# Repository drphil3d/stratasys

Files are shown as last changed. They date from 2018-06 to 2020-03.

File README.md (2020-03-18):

# Stratasys Reprap Project

Open Source Stratasys Conversion

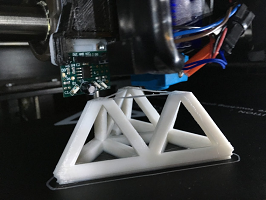
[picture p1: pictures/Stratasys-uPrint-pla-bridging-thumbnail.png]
Bridging Test


This was a long painful process, now that I've done the hard work it should be fairly easy for anyone to do this conversion. I'm not utilizing the stock hotends, they are designed for use with PC-ABS and other high temperature materials. At the moment I don't need dual extrusion, or the proprietary filament system which is far too complex. The results of this conversion is printer that makes consistent, strong parts with minimal effort.

If you plan to use the heated chamber above 40c you will need a water cooled hotend and extruder. I recommend using a Bondtech BMG - The Titan extruder was a nightmare, it requires disassembly to clear jams.

I recommend using a Ubis High Temperature hotend - 24v 90 Watt with a PT1000 and Thermistor
[Ubis Hotends](https://ubishotends.com/shop/xx9ppgi6moubdjx5kscfk8md4e8ecb)

##### Model Specific Firmware and Resources
   [Stratasys uPrint, uPrint SE / Plus](https://github.com/drphil3d/stratasys/tree/uPrint-SE)
   
   [Dimension 1200es SST / BST](https://github.com/drphil3d/stratasys/tree/Dimension-1200-SST)

Discussion
[Duet Forum](https://forum.duet3d.com/topic/10982/stratasys-uprint-retrofit-finally-complete/7)

#### Printer Control Board options

Ideally you want to use a board with decently powerful stepper drivers. Something in the 2amp range is preferable

##### DuetWifi
 -Pros
    Best option that matches the stepper drivers
    Sensorless Homing means no need to wire endstops
    Macro system is necessary for the extra features

 -Cons
    Display firmware doesn't support rotation of 90degrees
    Expensive
    
#### Klipper

 -Pros
   Use any board or combination of boards you want
   Super Fast Printing
   High Accuracy
   Customizable
   Macro Support
    
 -Cons
   Requires a raspberry pi or other embedded system

#### Marlin
 -Pros
   It works that was the first option I used on the uPrint

 -Cons
   Must be compiled and flashed every time you make a small change
   Most boards don't have stepper drivers that are powerful enough

#### Bake Oven temperature control
 The stock bake oven runs on 120VAC. Use an AC Solid State Rely to control the two heating elements. Keep in mind the heating elements can be wired for to operate at 120v ot 240v parallel or series.

 It is important that the fans spin whenever the heaters are energized.

 Make sure the heater safety shutoff switches operate correctly, If a fan stops spinning the heater will overheat without the shutoff switch. Do not remove them.

 This oven gets very hot under operation, I noticed the soldier on the OEM optical endstop PCB had melted and dripped down the board.
 Operating Temperature 0c - 75° C (167° F) Max

 Heating
    2x 120v DC 400 Watt (B075 CAT NO. FS2001G102) - Build Chamber Heaters one on each side
    2x 24V 0.48A Radial Blower Fans (blows air through the heating elements)
 Cooling   
    1x 24V Radial Blower Fan - Blows room temperature air onto the printhead and part from outside the build oven.

##### Gantry Information

 Depending on the model you may have more usable build area than what is immediately evident. The standard uPrint has a 152x152 build plate. However the printhead can reach outside of the build plate area to access more unused print volume. I believe the standard uPrint can accept two sizes of build platforms.

 Factory Specs
    uPrint 254 x 254 x 305 mm (10 x 10 x 12 in)
    Dimension SST 1200 SST X:254 Y:254 Z:305
 
 Actual Build Volume 
    uPrint X152 Y152 Z160

 Max Travel
    uPrint X280 Y262 Z150
    1200sst X:237.162 mm (9.33 in) Y:265.613 mm (10.45 in) Z:330.2 mm

 End Stops
    Use StallGuard sensorless homing and avoid all this madness, otherwise there are 2 optical endstops on each axis.

However another method is to tap into the test points the power distribution board if not already removed for the endstop signals   

  X-Min Y-Max Z-Max

Steps Per mm at 16x Microstepping
These seem to be accurate for the uPrint M92 X106.66 Y268 Z1011.99 E417
Z axis threaded rod is Imperial

Hardware
    XY 3mm belt pitch - 12mm GT3 Belts 16mm Linear Rods

 Belt / Gear Ratios
 uPrint
    X 16t x 60t x 20t (motor 16 tooth pulley) - (60 tooth pulley) - (20t drive shaft belt)
    Y 20t (20 tooth pulley) to (idler pulley)
    Z lead screw driven through motor mounted to bed
 1200 SST
    X (motor 16 tooth pulley) - (60 tooth pulley)
    Y (20 tooth pulley) to (idler pulley)
    Z (36 tooth pulley) to (36 tooth) to (big lead screw pitch unknown)
    
[More Hardware Specs](hardwarespecs.md)

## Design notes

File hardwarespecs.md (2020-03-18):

XY Axis Belt Specs

Gates 3MR-282-09 Belt
SKU 9390-4094
Part Number 3MR-282-09
Profile GT
Pitch	3 mm
Number of Teeth 94
Length (inch)	11.1
Length (mm)	282

Y Axis Small Belt

SDP A 6T53M280090
Bet Thickness 9mm
Pitch Length 840mm
Part Number: A 6R53M280090
Belt Type: Single Sided
Number of Grooves: 280
Belt Width: 9mm
Pitch Length: 840mm

GT®3 is an equivalent and direct replacement for GT®2 belts.
Neoprene - Nylon Covered, Fiberglass Reinforced
Breaking Strength: 158 N per 1 mm (113 lbf per 1/8 in.) 
Belt Width; not representative of the load-carrying capacity of the belt.
Working Tension:507 N for 25.4 mm belt (114 lbf for 1 in. belt).
Temperature Range: -34°C to +85°C (-30°F to +185°F)

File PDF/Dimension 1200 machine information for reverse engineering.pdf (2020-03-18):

Current Position The current X, Y and Z position in micro steps. X and Y = 16000 micro-steps per inch.
Z = 128000 micro-steps per inch.

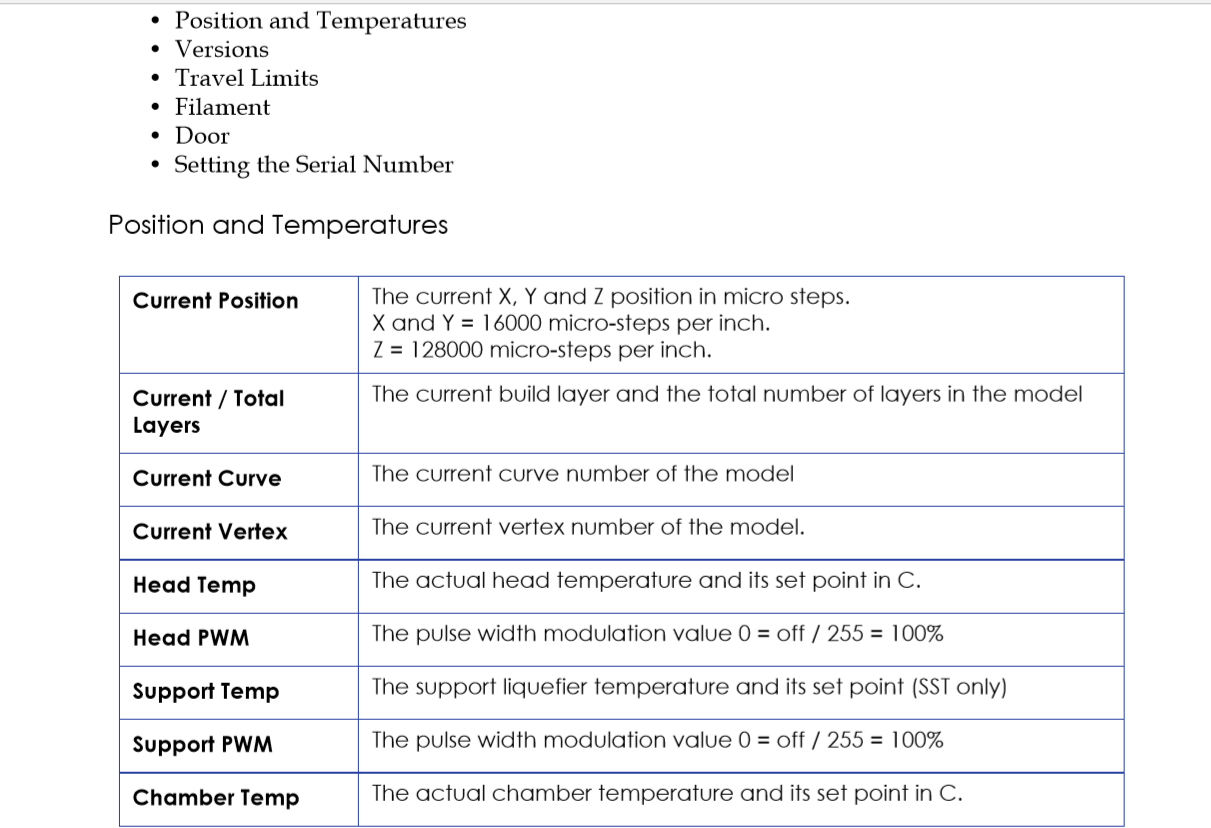
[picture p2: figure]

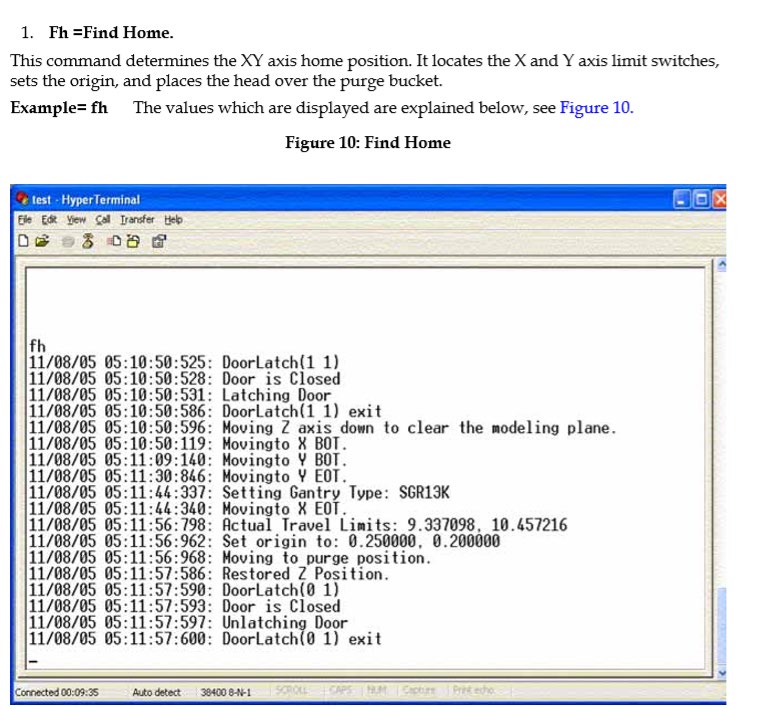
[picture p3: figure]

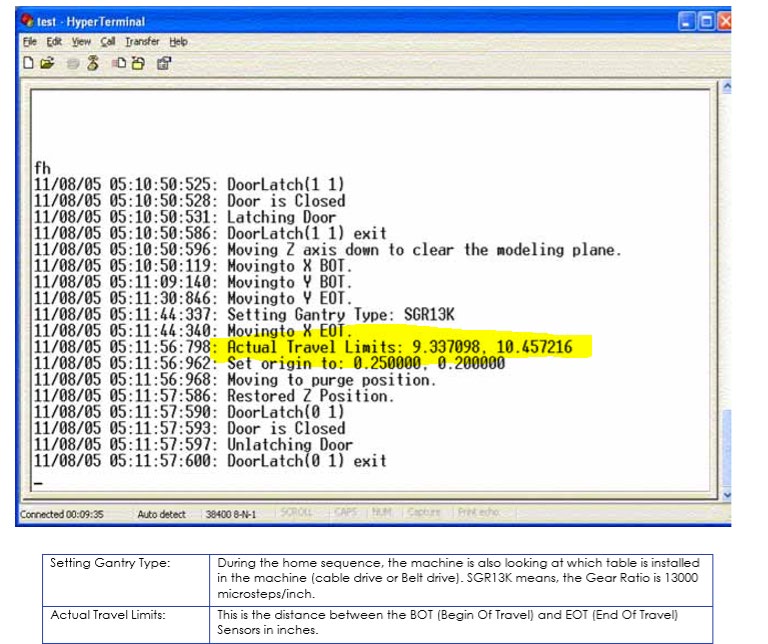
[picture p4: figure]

X:9.33 = 237.162mm Y: 10.45 = 265.613mm Origin 6.35 mm 5.08

X EOT 9.337098
Y EOT 10.457216

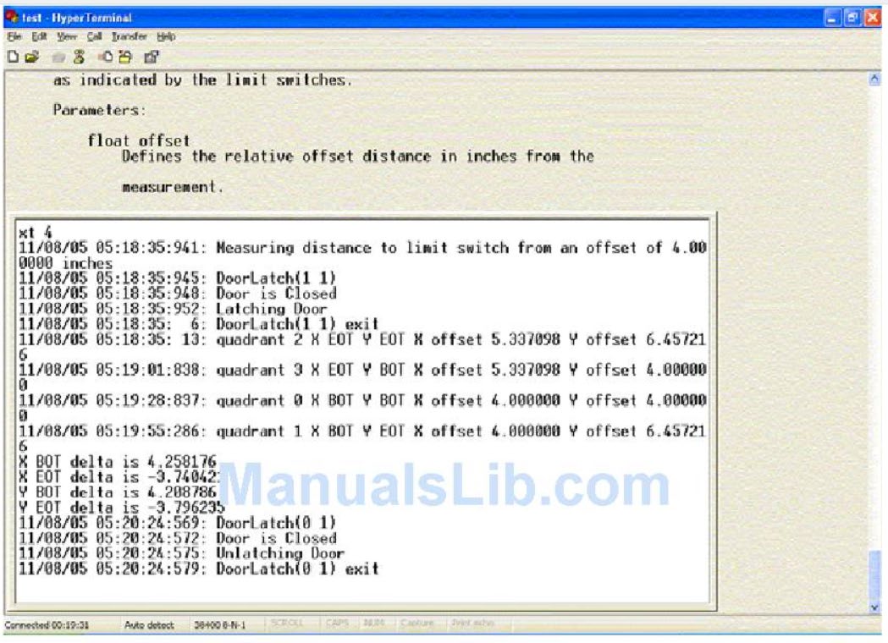
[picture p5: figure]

2 X offset 135.38
0 X offset 101.6 Y offset 101.6
1 X offset 101.6 Y offset 164.0131

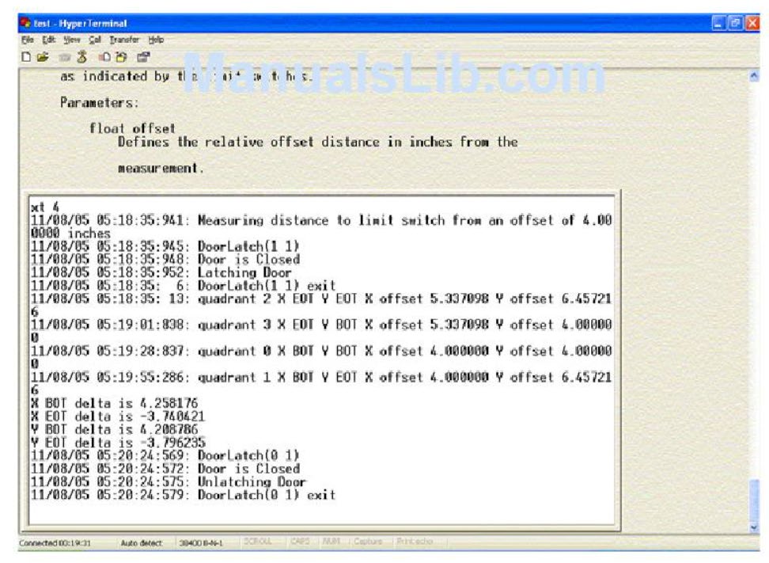
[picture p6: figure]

### 5. xt=Test XY Limits

Tests the XY axis by moving from corner to corner, stopping at each corner and measuring the offset against the actual position as indicated by the limit switches.
The command can be used for testing the Z-Stage. To do so, repeat the tz command at least 2 times and compare the X BOT delta values, X EOT delta values, Y BOT delta values and the Y EOT delta values. Parameters: Float Offset: Defines the relative offset distance in inches from the limit switch. The offset is the starting point for the measurement. Example= xt 2.0 2.0= distance, where the machine starts to look for the sensors. For repeating the command, type in the following: rt 2 1 "xt 2.0”. For more information see the rt command (item #8) in this manual.
Figure 13: Text XY limits

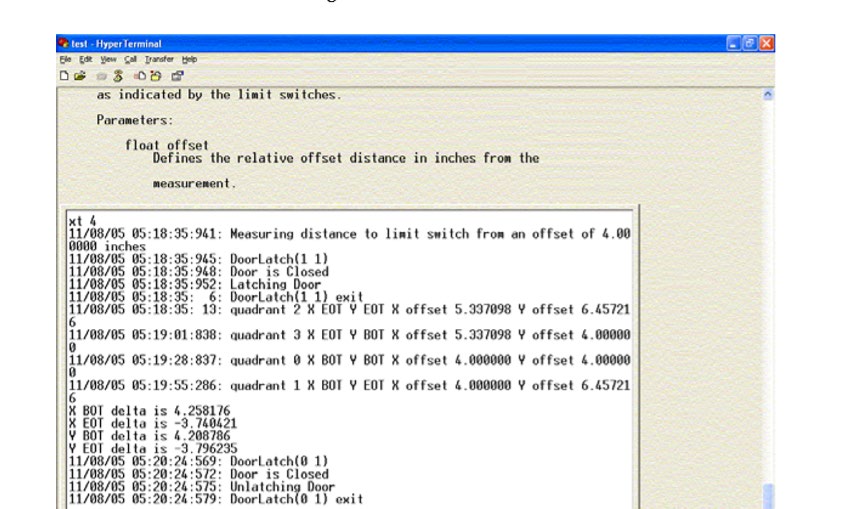
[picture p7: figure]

10. mx = move x This command moves the head in the X axis. Parameters: Float Position: This is the position it moves to, in inches, when the command is sent from the Console and in device units when the command is sent through the DPM.
Example: mx 3.0 (moves the X-Axis 3 inches away from the X-Home sensor

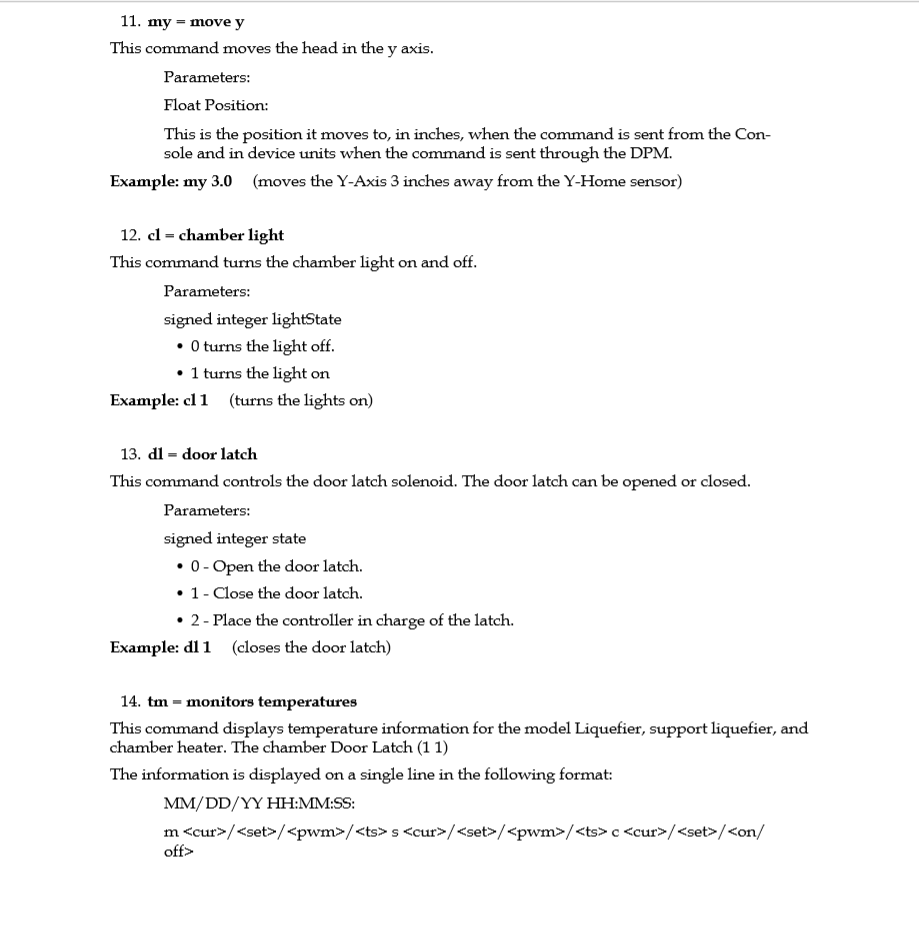
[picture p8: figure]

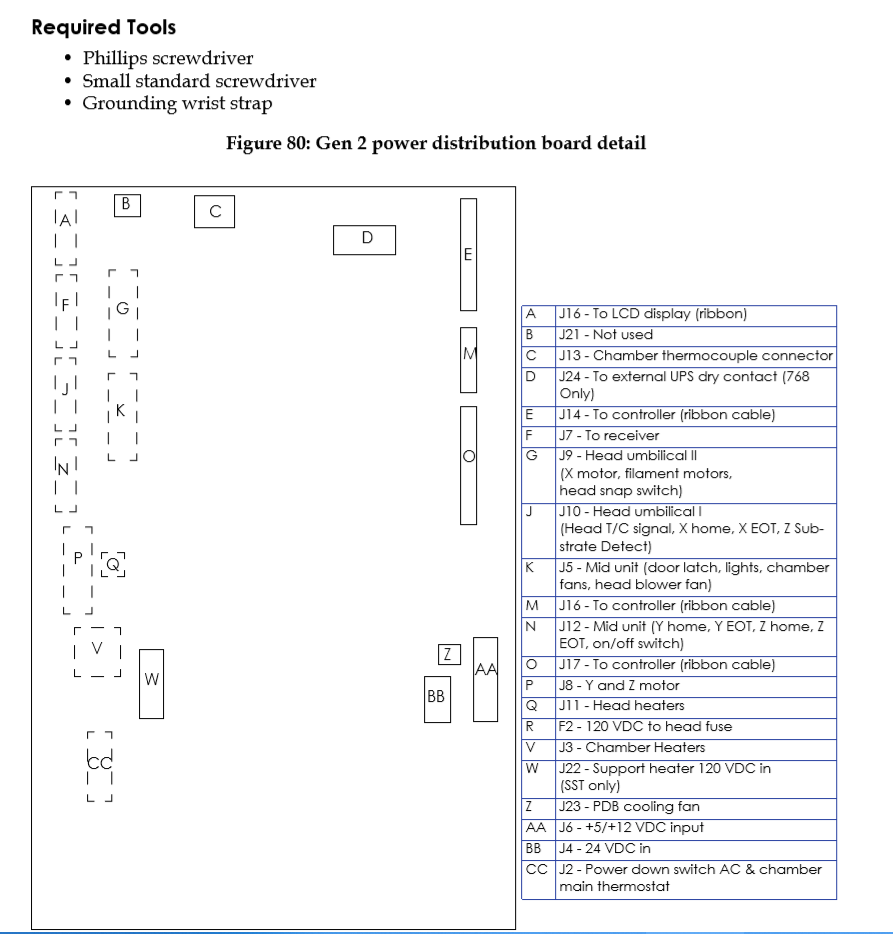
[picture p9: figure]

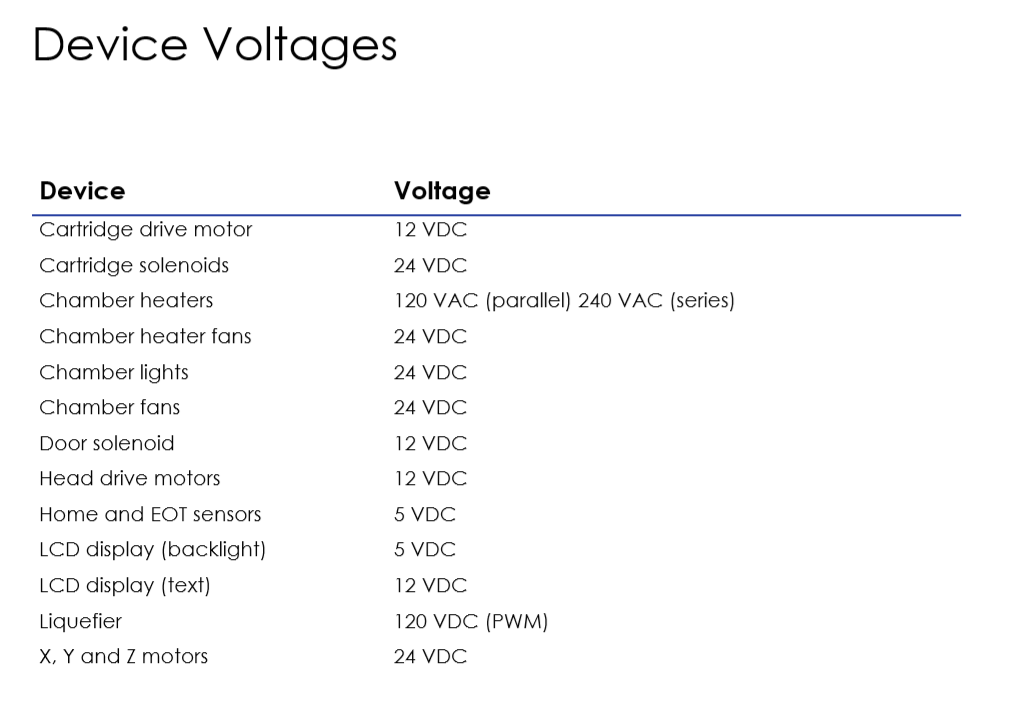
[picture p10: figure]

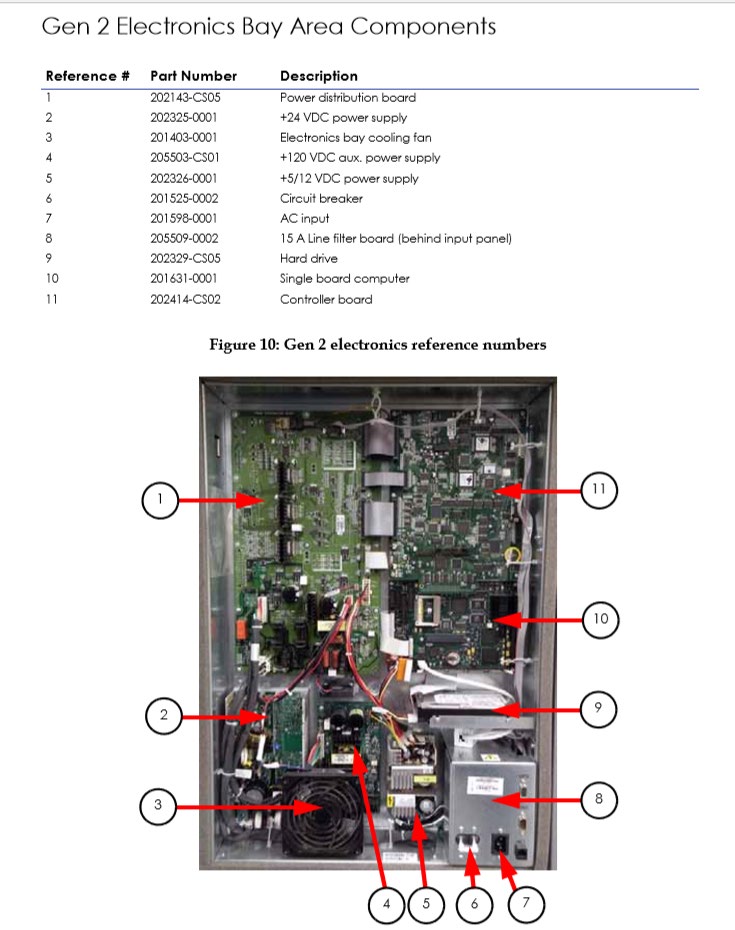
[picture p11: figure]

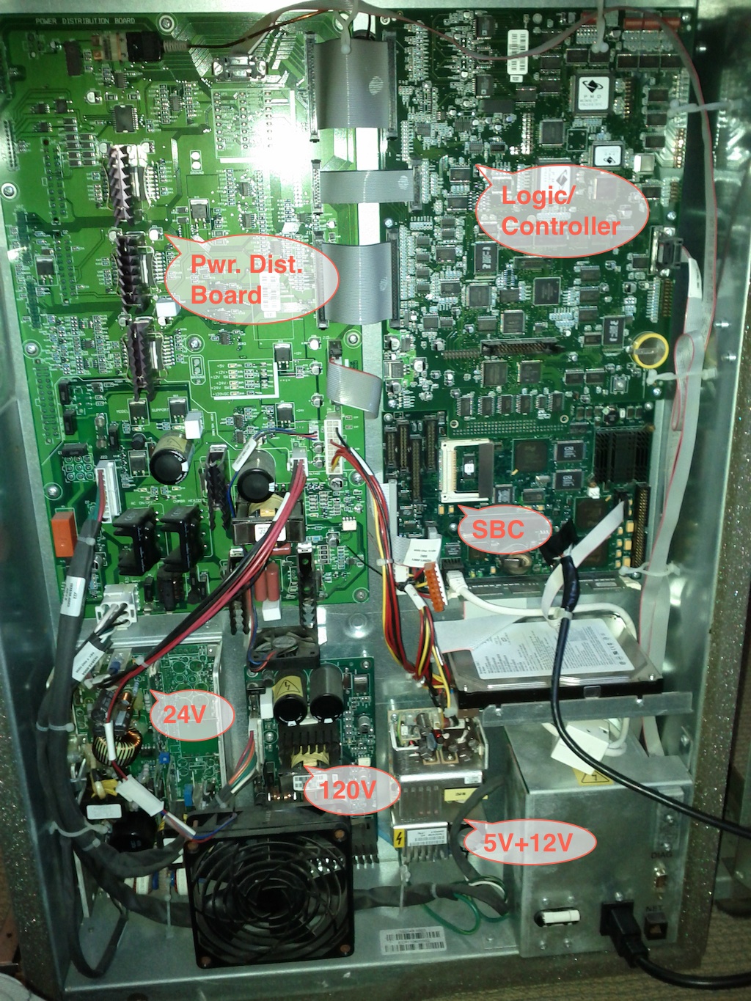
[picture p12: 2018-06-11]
pictures/dimension-sst-electronics-bay.jpg

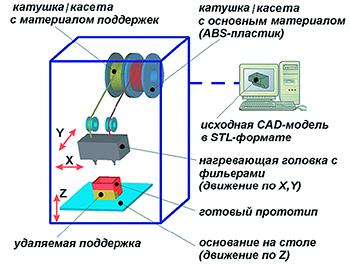
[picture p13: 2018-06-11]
pictures/stratasys_05.jpg

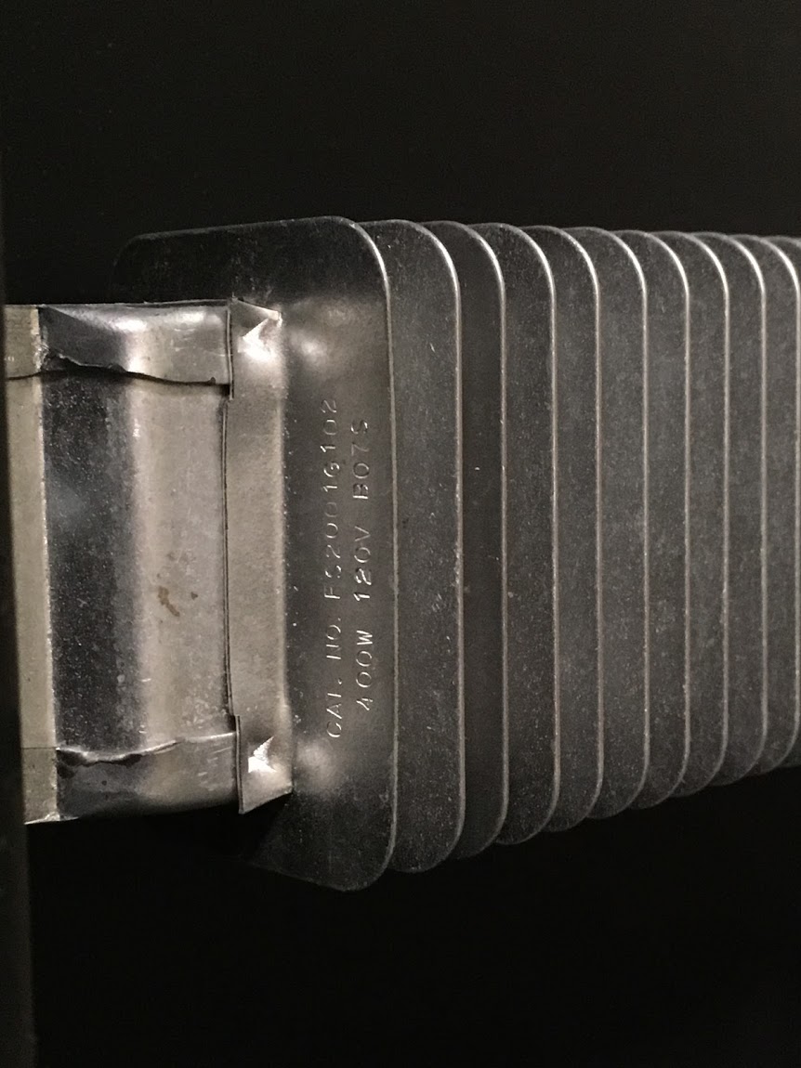
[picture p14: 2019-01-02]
pictures/heater.JPG

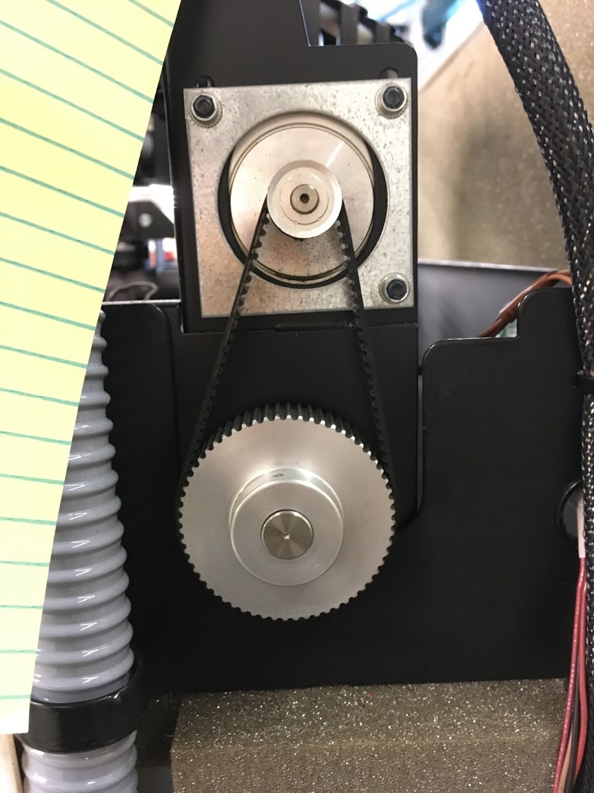
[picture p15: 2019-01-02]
pictures/y axis.JPG

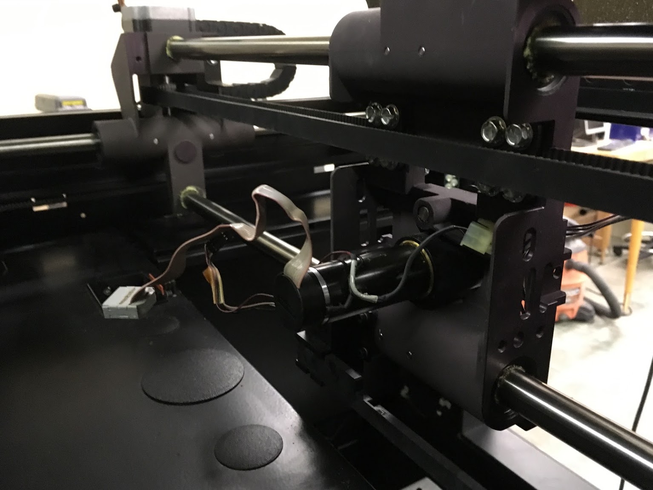
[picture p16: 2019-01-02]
pictures/y axis extruder.JPG

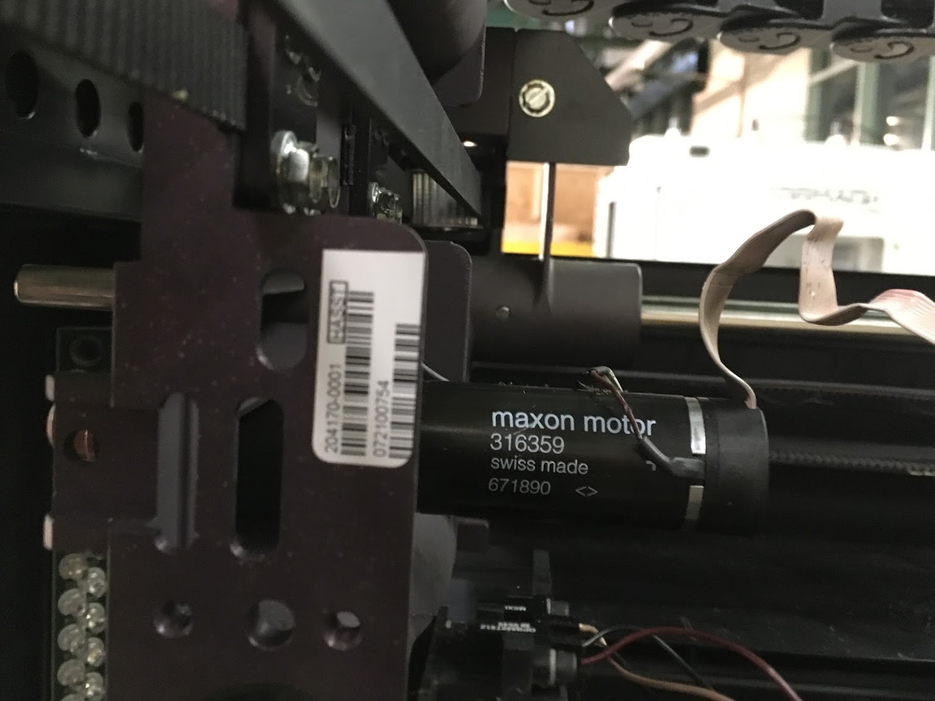
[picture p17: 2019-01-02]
pictures/extruder.JPG

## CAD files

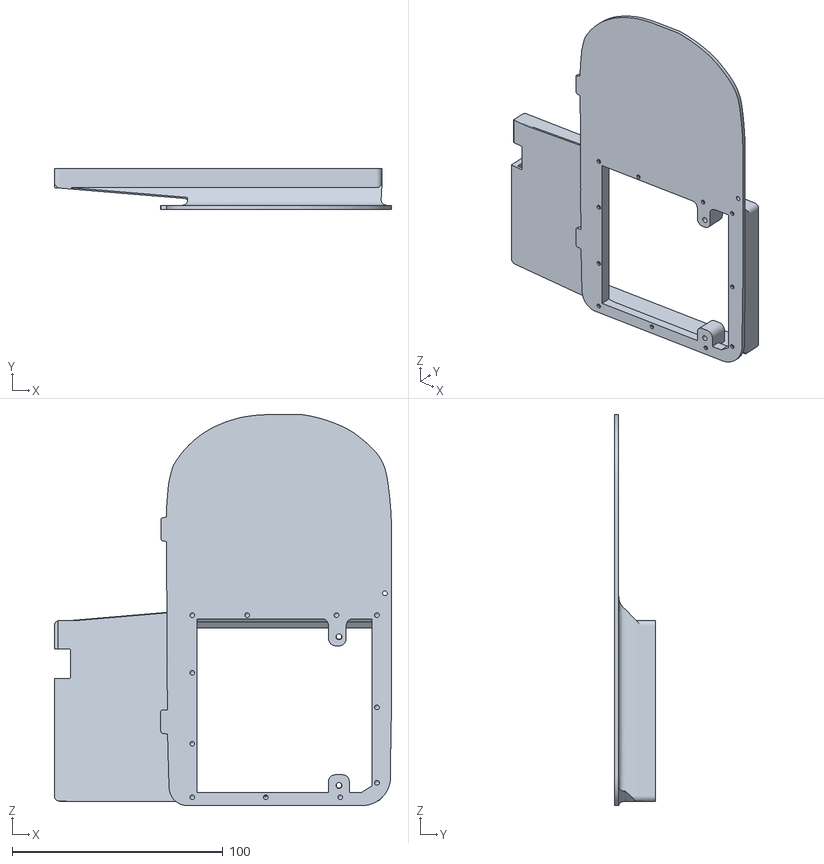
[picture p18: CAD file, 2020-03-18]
STL Files/Stratasys Panel Due.stl
160.2 x 19.2 x 185.6

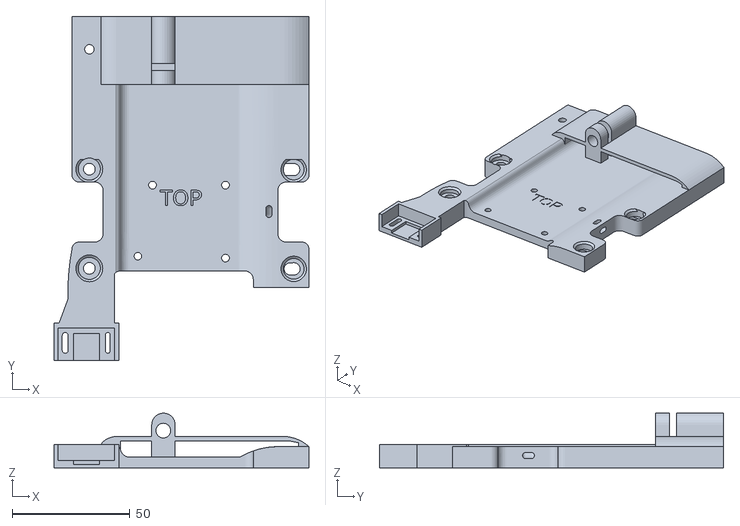
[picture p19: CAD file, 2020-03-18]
STL Files/Stratasys Printhead Mount.stl
108.3 x 146.2 x 23.2

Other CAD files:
CAD Files/6 to 4 mm adapter.f3d
CAD Files/EndStop Mount X+Z.f3d
CAD Files/EndStop Print Head Mount.f3d
CAD Files/Endstop Switch Mount.f3z
CAD Files/Print Head extruder Mounting Bracket.f3z
CAD Files/enstop mount.f3d
CAD Files/uPrint Front LCD.f3d
CAD Files/uPrint Hotend Adapter.f3d
CAD Files/uPrint Hotend Adapter.f3z

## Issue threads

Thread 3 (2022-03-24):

Belt titles are wrong

LazyTeenStudios, 2022-03-24:
In the readMe file the description for the small Y belt is under the title “XY axis belt specs” while the XY belt info is under the title “Y axis small belt.”

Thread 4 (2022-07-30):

Safety Thermistor Wiring

S1L3NTANG3L, 2022-07-30:
Just curious on how you ended up wiring the safety thermistors for the chamber heaters. Did you wire them in series with the heaters?

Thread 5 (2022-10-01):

Endstops

S1L3NTANG3L, 2022-10-01:
Hi
Did you use the oem optical end stops or did you replace them? (Uprint SE specifically).
Thanks

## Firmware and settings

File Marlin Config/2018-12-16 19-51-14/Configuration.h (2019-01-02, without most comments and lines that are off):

#pragma once
#define CONFIGURATION_H_VERSION 020000
#define STRING_CONFIG_H_AUTHOR "Dr. Phil3D"             // Who made the changes.
#define SHOW_BOOTSCREEN
#define STRING_SPLASH_LINE1 SHORT_BUILD_VERSION // will be shown during bootup in line 1
#define STRING_SPLASH_LINE2 WEBSITE_URL         // will be shown during bootup in line 2
#define SERIAL_PORT 0
#define BAUDRATE 250000
  #define MOTHERBOARD BOARD_EINSY_RETRO
#define CUSTOM_MACHINE_NAME "Stratasys"
#define MACHINE_UUID "b1910d4c-db07-11e8-9f8b-f2801f1b9fd1"
#define EXTRUDERS 1
#define DEFAULT_NOMINAL_FILAMENT_DIA 1.75
#define POWER_SUPPLY 0
#define TEMP_SENSOR_0 5
#define TEMP_SENSOR_1 0
#define TEMP_SENSOR_2 0
#define TEMP_SENSOR_3 0
#define TEMP_SENSOR_4 0
#define TEMP_SENSOR_5 0
#define TEMP_SENSOR_BED 1
#define TEMP_SENSOR_CHAMBER 0
#define DUMMY_THERMISTOR_998_VALUE 25
#define DUMMY_THERMISTOR_999_VALUE 100
#define MAX_REDUNDANT_TEMP_SENSOR_DIFF 10
#define TEMP_RESIDENCY_TIME 10  // (seconds)
#define TEMP_HYSTERESIS 3       // (degC) range of +/- temperatures considered "close" to the target one
#define TEMP_WINDOW     1       // (degC) Window around target to start the residency timer x degC early.
#define TEMP_BED_RESIDENCY_TIME 10  // (seconds)
#define TEMP_BED_HYSTERESIS 3       // (degC) range of +/- temperatures considered "close" to the target one
#define TEMP_BED_WINDOW     1       // (degC) Window around target to start the residency timer x degC early.
#define HEATER_0_MINTEMP 5
#define HEATER_1_MINTEMP 5
#define HEATER_2_MINTEMP 5
#define HEATER_3_MINTEMP 5
#define HEATER_4_MINTEMP 5
#define HEATER_5_MINTEMP 5
#define BED_MINTEMP 5
#define HEATER_0_MAXTEMP 300
#define HEATER_1_MAXTEMP 275
#define HEATER_2_MAXTEMP 275
#define HEATER_3_MAXTEMP 275
#define HEATER_4_MAXTEMP 275
#define HEATER_5_MAXTEMP 70
#define BED_MAXTEMP 70
#define PIDTEMP
#define BANG_MAX 255     // Limits current to nozzle while in bang-bang mode; 255=full current
#define PID_MAX BANG_MAX // Limits current to nozzle while PID is active (see PID_FUNCTIONAL_RANGE below); 255=full current
#define PID_K1 0.95      // Smoothing factor within any PID loop
  #define PID_AUTOTUNE_MENU       // Add PID Autotune to the LCD "Temperature" menu to run M303 and apply the result.
  #define PID_FUNCTIONAL_RANGE 10 // If the temperature difference between the target temperature and the actual temperature
  #define DEFAULT_Kp 22.2
  #define DEFAULT_Ki 1.08
  #define DEFAULT_Kd 114
#define MAX_BED_POWER 255 // limits duty cycle to bed; 255=full current
#define PREVENT_COLD_EXTRUSION
#define EXTRUDE_MINTEMP 170
#define PREVENT_LENGTHY_EXTRUDE
#define EXTRUDE_MAXLENGTH 200
#define THERMAL_PROTECTION_HOTENDS // Enable thermal protection for all extruders
#define THERMAL_PROTECTION_BED     // Enable thermal protection for the heated bed
#define USE_XMIN_PLUG
#define USE_YMAX_PLUG
#define USE_ZMAX_PLUG
#define ENDSTOPPULLUPS
  #define ENDSTOPPULLDOWN_ZMIN_PROBE
#define X_MIN_ENDSTOP_INVERTING true  // set to true to invert the logic of the endstop.
#define Y_MIN_ENDSTOP_INVERTING false // set to true to invert the logic of the endstop.
#define Z_MIN_ENDSTOP_INVERTING false // set to true to invert the logic of the endstop.
#define X_MAX_ENDSTOP_INVERTING false // set to true to invert the logic of the endstop.
#define Y_MAX_ENDSTOP_INVERTING true  // set to true to invert the logic of the endstop.
#define Z_MAX_ENDSTOP_INVERTING true  // set to true to invert the logic of the endstop.
#define Z_MIN_PROBE_ENDSTOP_INVERTING false // set to true to invert the logic of the probe.
#define X_DRIVER_TYPE  TMC2130
#define Y_DRIVER_TYPE  TMC2130
#define Z_DRIVER_TYPE  TMC2130
#define E0_DRIVER_TYPE TMC2130
#define DEFAULT_AXIS_STEPS_PER_UNIT   { 53.33, 133.75, 1011.89, 418 }
#define DEFAULT_MAX_FEEDRATE          { 125, 125, 10, 45 }
#define DEFAULT_MAX_ACCELERATION      { 1000, 1000, 200, 5000 }
#define DEFAULT_ACCELERATION          1000    // X, Y, Z and E acceleration for printing moves
#define DEFAULT_RETRACT_ACCELERATION  1000    // E acceleration for retracts
#define DEFAULT_TRAVEL_ACCELERATION   1000    // X, Y, Z acceleration for travel (non printing) moves
#define DEFAULT_XJERK                 10.0
#define DEFAULT_YJERK                 8
#define DEFAULT_ZJERK                  0.3
#define DEFAULT_EJERK                  4.5
#define S_CURVE_ACCELERATION
#define Z_MIN_PROBE_ENDSTOP
#define PROBE_MANUALLY
#define X_PROBE_OFFSET_FROM_EXTRUDER 0   // X offset: -left  +right  [of the nozzle]
#define Y_PROBE_OFFSET_FROM_EXTRUDER 0   // Y offset: -front +behind [the nozzle]
#define Z_PROBE_OFFSET_FROM_EXTRUDER 0     // Z offset: -below +above  [the nozzle]
#define MIN_PROBE_EDGE 45
#define XY_PROBE_SPEED 7000
#define Z_PROBE_SPEED_FAST HOMING_FEEDRATE_Z
#define Z_PROBE_SPEED_SLOW (Z_PROBE_SPEED_FAST / 2)
#define MULTIPLE_PROBING 2
#define Z_CLEARANCE_DEPLOY_PROBE   10 // Z Clearance for Deploy/Stow
#define Z_CLEARANCE_BETWEEN_PROBES  5 // Z Clearance between probe points
#define Z_CLEARANCE_MULTI_PROBE     5 // Z Clearance between multiple probes
#define Z_PROBE_LOW_POINT          -25 // Farthest distance below the trigger-point to go before stopping
#define Z_PROBE_OFFSET_RANGE_MIN -25
#define Z_PROBE_OFFSET_RANGE_MAX 25
#define X_ENABLE_ON 0
#define Y_ENABLE_ON 0
#define Z_ENABLE_ON 0
#define E_ENABLE_ON 0 // For all extruders
#define DISABLE_X false
#define DISABLE_Y false
#define DISABLE_Z false
#define DISABLE_E false             // For all extruders
#define INVERT_X_DIR false
#define INVERT_Y_DIR false
#define INVERT_Z_DIR false
#define INVERT_E0_DIR true
#define INVERT_E1_DIR false
#define INVERT_E2_DIR false
#define INVERT_E3_DIR false
#define INVERT_E4_DIR false
#define INVERT_E5_DIR false
#define UNKNOWN_Z_NO_RAISE   // Don't raise Z (lower the bed) if Z is "unknown." For beds that fall when Z is powered off.
#define X_HOME_DIR -1
#define Y_HOME_DIR 1
#define Z_HOME_DIR 1
#define X_BED_SIZE 280
#define Y_BED_SIZE 262
#define X_MIN_POS 0
#define Y_MIN_POS 0
#define Z_MIN_POS 0
#define X_MAX_POS X_BED_SIZE
#define Y_MAX_POS Y_BED_SIZE
#define Z_MAX_POS 150
#define MIN_SOFTWARE_ENDSTOPS
  #define MIN_SOFTWARE_ENDSTOP_X
  #define MIN_SOFTWARE_ENDSTOP_Y
  #define MIN_SOFTWARE_ENDSTOP_Z
#define MAX_SOFTWARE_ENDSTOPS
  #define MAX_SOFTWARE_ENDSTOP_X
  #define MAX_SOFTWARE_ENDSTOP_Y
  #define MAX_SOFTWARE_ENDSTOP_Z
  #define SOFT_ENDSTOPS_MENU_ITEM    // Enable/Disable software endstops from the LCD
#define MESH_BED_LEVELING
#define RESTORE_LEVELING_AFTER_G28
#define DEBUG_LEVELING_FEATURE
  #define SEGMENT_LEVELED_MOVES
  #define LEVELED_SEGMENT_LENGTH 5.0 // (mm) Length of all segments (except the last one)
  #define G26_MESH_VALIDATION
    #define MESH_TEST_NOZZLE_SIZE    0.4  // (mm) Diameter of primary nozzle.
    #define MESH_TEST_LAYER_HEIGHT   0.2  // (mm) Default layer height for the G26 Mesh Validation Tool.
    #define MESH_TEST_HOTEND_TEMP  205.0  // (°C) Default nozzle temperature for the G26 Mesh Validation Tool.
    #define MESH_TEST_BED_TEMP      0     // (°C) Default bed temperature for the G26 Mesh Validation Tool.
  #define MESH_INSET 100         // Set Mesh bounds as an inset region of the bed
  #define GRID_MAX_POINTS_X 2    // Don't use more than 7 points per axis, implementation limited.
  #define GRID_MAX_POINTS_Y 2
#define LCD_BED_LEVELING
  #define MESH_EDIT_Z_STEP  0.025 // (mm) Step size while manually probing Z axis.
  #define LCD_PROBE_Z_RANGE 30    // (mm) Z Range centered on Z_MIN_POS for LCD Z adjustment
  #define MESH_EDIT_MENU          // Add a menu to edit mesh points
#define Z_SAFE_HOMING
  #define Z_SAFE_HOMING_X_POINT 42                    // X point for Z homing when homing all axes (G28).
  #define Z_SAFE_HOMING_Y_POINT 250                   // Y point for Z homing when homing all axes (G28).
#define HOMING_FEEDRATE_XY (60*60)
#define HOMING_FEEDRATE_Z  (20*60)
#define VALIDATE_HOMING_ENDSTOPS
#define EEPROM_SETTINGS   // Enable for M500 and M501 commands
#define EEPROM_CHITCHAT   // Give feedback on EEPROM commands. Disable to save PROGMEM.
#define HOST_KEEPALIVE_FEATURE        // Disable this if your host doesn't like keepalive messages
#define DEFAULT_KEEPALIVE_INTERVAL 2  // Number of seconds between "busy" messages. Set with M113.
#define BUSY_WHILE_HEATING            // Some hosts require "busy" messages even during heating
#define PREHEAT_1_LABEL       "PLA"
#define PREHEAT_1_TEMP_HOTEND 200
#define PREHEAT_1_TEMP_BED     30
#define PREHEAT_1_FAN_SPEED     255 // Value from 0 to 255
#define PREHEAT_2_LABEL       "ABSplus-P430"
#define PREHEAT_2_TEMP_HOTEND 225
#define PREHEAT_2_TEMP_BED    60
#define PREHEAT_2_FAN_SPEED     255 // Value from 0 to 255
#define NOZZLE_PARK_FEATURE
  #define NOZZLE_PARK_POINT { (X_MIN_POS + 42), (Y_MAX_POS - 20), 5 }
  #define NOZZLE_PARK_XY_FEEDRATE 45    // X and Y axes feedrate in mm/s (also used for delta printers Z axis)
  #define NOZZLE_PARK_Z_FEEDRATE 8      // Z axis feedrate in mm/s (not used for delta printers)
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

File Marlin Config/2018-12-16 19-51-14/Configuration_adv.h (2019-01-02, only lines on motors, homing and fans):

#define E0_AUTO_FAN_PIN 6
#define E1_AUTO_FAN_PIN -1
#define E2_AUTO_FAN_PIN -1
#define E3_AUTO_FAN_PIN -1
#define E4_AUTO_FAN_PIN -1
#define E5_AUTO_FAN_PIN -1
#define CHAMBER_AUTO_FAN_PIN -1
#define X_HOME_BUMP_MM 0
#define Y_HOME_BUMP_MM 0
#define Z_HOME_BUMP_MM 2
#define HOMING_BUMP_DIVISOR { 2, 2, 2 }  // Re-Bump Speed Divisor (Divides the Homing Feedrate)
#define HOME_Y_BEFORE_X
#define MICROSTEP_MODES { 16, 16, 16, 16, 16, 16 } // [1,2,4,8,16]
#define DIGIPOT_I2C_MOTOR_CURRENTS { 1.0, 1.0, 1.0, 1.0, 1.0, 1.0, 1.0, 1.0 }  //  AZTEEG_X3_PRO
#define LIN_ADVANCE
  #define LIN_ADVANCE_K 0.06  // Unit: mm compression per 1mm/s extruder speed
#define ADVANCED_PAUSE_FEATURE
  #define ADVANCED_PAUSE_PURGE_FEEDRATE        3  // (mm/s) Extrude feedrate (after loading). Should be slower than load feedrate.
  #define ADVANCED_PAUSE_PURGE_LENGTH         40  // (mm) Length to extrude after loading.
  #define X_CURRENT          500  // rms current in mA. Multiply by 1.41 for peak current.
  #define X_MICROSTEPS        16  // 0..256
  #define Y_CURRENT          500
  #define Y_MICROSTEPS        16
  #define Z_CURRENT          750
  #define Z_MICROSTEPS        16
  #define X2_CURRENT         800
  #define X2_MICROSTEPS       16
  #define Y2_CURRENT         800
  #define Y2_MICROSTEPS       16
  #define Z2_CURRENT         800
  #define Z2_MICROSTEPS       16
  #define Z3_CURRENT         800
  #define Z3_MICROSTEPS       16
  #define E0_CURRENT         600
  #define E0_MICROSTEPS       16
  #define E1_CURRENT         800
  #define E1_MICROSTEPS       16
  #define E2_CURRENT         800
  #define E2_MICROSTEPS       16
  #define E3_CURRENT         800
  #define E3_MICROSTEPS       16
  #define E4_CURRENT         800
  #define E4_MICROSTEPS       16
  #define E5_CURRENT         800
  #define E5_MICROSTEPS       16
    #define CURRENT_STEP_DOWN     50  // [mA]
    #define REPORT_CURRENT_CHANGE
  #define X_HYBRID_THRESHOLD     100  // [mm/s]
  #define X2_HYBRID_THRESHOLD    100
  #define Y_HYBRID_THRESHOLD     100
  #define Y2_HYBRID_THRESHOLD    100
  #define Z_HYBRID_THRESHOLD       3
  #define Z2_HYBRID_THRESHOLD      3
  #define Z3_HYBRID_THRESHOLD      3
  #define E0_HYBRID_THRESHOLD     30
  #define E1_HYBRID_THRESHOLD     30
  #define E2_HYBRID_THRESHOLD     30
  #define E3_HYBRID_THRESHOLD     30
  #define E4_HYBRID_THRESHOLD     30
  #define E5_HYBRID_THRESHOLD     30
  #define SENSORLESS_HOMING   // TMC2130 only
    #define X_STALL_SENSITIVITY  0
    #define Y_STALL_SENSITIVITY  -15

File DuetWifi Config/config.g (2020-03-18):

; Configuration file for Duet WiFi (firmware version 1.21)
; executed by the firmware on start-up
;
;Stratasys uPrint Configuration 6-20-2019
;
; General preferences
G90                                      ; Send absolute coordinates...
M83                                      ; ...but relative extruder moves

; Network
;M552 S1 P"SET NETWORK NAME"

; Drives
M569 P0 S0                               ; Physical drive 0 goes forwards
M569 P1 S0                               ; Physical drive 1 goes forwards
M569 P2 S0                               ; Physical drive 2 goes forwards
M569 P3 S1                               ; Physical drive 3 goes forwards
M350 X32 Y32 Z16 E16 I1                  ; Configure microstepping with interpolation
;M92  X53.33 Y134 Z1011.99 E417            ; Set steps per mm
M92 X106.66 Y268 Z1011.99 E417
M566 X1500 Y1200.00 Z25 E1500      ; Set maximum instantaneous speed changes (mm/min)
M203 X24000 Y24000.00 Z650 E1200.00   ; Set maximum speeds (mm/min)
M201 X1000 Y800 Z50 E3000        ; Set accelerations (mm/s^2)
M906 X950 Y950 Z950 E500 I35 ; Set motor currents (mA) and motor idle factor in per cent
M84 S30                                  ; Set idle timeout

; Axis Limits
M208 X0 Y0 Z0 S1                         ; Set axis minima
M208 X262 Y265 Z185 S0                   ; Set axis maxima

; Endstops
M574 X1 Y2 S1                            ; Set active high endstops

; Z-Probe
M574 Z2 S1                              ; Set endstops controlled by probe
M558 P1 H10 F120 T6000                  ; Set Z probe type to unmodulated and the dive height + speeds
G31 P520 X-38 Y18 Z1.982                ; Set Z probe trigger value, offset and trigger height
;M557 X88:260 Y0:157 S50                 ; Define mesh grid

; Heaters
;M140 H-1                                 ; Disable heated bed
;M305 P0 T100000 B4725 C7.060000e-8 R4700 ; Set thermistor + ADC parameters for heater 0
;M143 H0 S55                              ; Set temperature limit for heater 0 to 50C
M305 P1 T100000 B4138 R4700              ; Set thermistor + ADC parameters for heater 1
M143 H1 S280                             ; Set temperature limit for heater 1 to 280C

; Fans
M106 P0 S0 I0 F500 H1 T45                ; Set fan 0 value, PWM signal inversion and frequency. Thermostatic control is turned on
M106 P1 S1 I0 F500 H0 T40
M106 P2 S1 I0 F500 H0 T40               ; Set fan 1 value, PWM signal inversion and frequency. Thermostatic control is turned on

; Chamber
M141 H0                                    ; Assign chamber heater to heater 0
M143 H0 S55                                ; Set temperature limit for heater 0 to 55C
M307 H0 A50 D90 B1                         ; use bang-bang heater with 60 seconds dead time
M305 P0 T100000 B4725 C7.060000e-8 R4700   ; Set thermistor + ADC parameters for chamber mid thermistor

; Tools
M563 P0 D0 H1                            ; Define tool 0
G10 P0 X0 Y0 Z0                          ; Set tool 0 axis offsets
G10 P0 R0 S0                             ; Set initial tool 0 active and standby temperatures to 0C

; Automatic saving after power loss is not enabled

; Custom settings are not configured

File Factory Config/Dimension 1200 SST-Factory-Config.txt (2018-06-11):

Stratasys Config
usefull info 
ZAXISHOMEOFFSET=-0.038000



XAXISPOWER=20000
YAXISPOWER=20000
ZAXISPOWER=22000

Thu Jan  1 01:54:25 CST 1998
 
Version  7.2
Build    1924
 
-----  machine.cfg ----------
# edited for pencil testing.  return value to 1500
ZAXISHOMEOFFSET=-0.038000
XYAXISID=UNKNOWN
YLASH=0.001,0.001,0.001,0.001
GENDER=SCHOONER
XCORR=0
#### LAST LINE
SERIALNUMBER=P01870
PCAL=7.5130,7.5160,7.5270,7.60,10.6160,10.6550
UPNPCONFIG=1
UDN=sst768P01870
LANGUAGE=en_US
-----  system.cfg ----------
ZCLEARANCE=-0.0003
TIPOFFSET=0.2530,-0.0010
CALIBRATED=1 
 
-----  modeler.cfg ----------
SPTHEADMOTORKP=1000
SPTHEADMOTORKI=30
SPTHEADMOTORKD=1100
SPTHEADMOTORAC=500
SPTHEADMOTORIL=9999
SPTHEADMOTORDS=25
MDLHEADMOTORKP=1000
MDLHEADMOTORKI=30
MDLHEADMOTORKD=1100
MDLHEADMOTORAC=500
MDLHEADMOTORIL=9999
MDLHEADMOTORDS=25
SUPPREPURGEDELAY=0
SUPPREPURGEROLLBACK=0
SPTLONGPURGERATE=10000
SPTLONGPURGETIME=35
SPTLONGPURGERBRATE=40000
SPTLONGPURGERBDIST=0
SPTSTDPURGERATE=12000
SPTSTDPURGETIME=25
SPTSTDPURGERBRATE=40000
SPTSTDPURGERBDIST=-210
SUPPOSTPURGEDELAY=0
SUPADDROLLBACK=-700
IDLEPURGEDELAY=5
TIPIDLETIMEOUT=200
MDLPREPURGEDELAY=0
MDLPREPURGEROLLBACK=0
MDLLONGPURGERATE=20000
MDLLONGPURGETIME=50
MDLLONGPURGERBRATE=40000
MDLLONGPURGERBDIST=-10
MDLSTDPURGERATE=10000
MDLSTDPURGETIME=30
MDLSTDPURGERBRATE=40000
MDLSTDPURGERBDIST=-270
MDLPOSTPURGEDELAY=0
MDLADDROLLBACK=-700
KTEMPERATURETODAC=7
TIMETEMPERATUREINTEGRATION=95 
KPROPORTIONALACTION=30
TDERIVITIVE=4
HOTTEMPERATURE=2700
COOLTEMPERATURE=2700
MDLTEMPTOL=70
MDLHIGHTEMPALARM=3000
MDLLOWTEMPALARM=2299
SUPHOTTEMPERATURE=2500
SUPCOOLTEMPERATURE=2100
SUPTEMPTOL=70
SUPHIGHTEMPALARM=3000
SUPLOWTEMPALARM=2000
SYSTEMREVISION=1
HMRUNTIME=6000
XAXISPOWER=20000
YAXISPOWER=20000
ZAXISPOWER=22000
GLUELESSRATE=40
GLUELESSACCELERATION=0
ZAXISVELOCITY=0
ZAXISACCELERATION=0
FHCRAWL=0
FHVELOCITY=0
LCLOADSPEED=10000
LCDETECTSPEED=20000
UCBACKOUTSPEED=10000
CASSRETRYLIMIT=3
CASSFAILLIMIT=60
XPURGEPOSITION=0
XBRUSHPOSITION=0
YPURGEPOSITION=0
YBRUSHPOSITION=0
TWBRUSHLEN=0
TWBRUSHWID=0
TWWIPELEN=0
TWWIPEWID=0
TWWIPESTEP=0
SUPSETBACKTEMP=1025
 
-----  modeler2.cfg ----------
################################################################################
#
#       Copyright (c) 2005-2006, Stratasys Inc.
#       All Rights Reserved Worldwide.
#
#       MODELER2.CFG FILE FOR Schooner and Spinnaker
#
#       %full_name: %
#       %derived_by: %
#       %date_created: %
#
################################################################################

# History:
# Rev B:  Added model temperature setback parameter.  BND 12-14-07
# Rev C:  Increased model setback temp from 200 to 255.  BND 2-20-08
#
# This file contains the following information:
#   head motor PID values
#   select head purge parameters
#   head PID control parameters
#   autoload parameters
#   Stepper Motor Currents:
#   XYZ Axis Speed Parameters:
#   Purge and Tip Wipe Locations:
# ------------------------------------------------
SP THE AD MOTOR KP=1000
SPTHEADMOTORKI=13
SPTHEADMOTORKD=1056
SPTHEADMOTORAC=2876
SPTHEADMOTORIL=9999
SPTHEADMOTORDS=10
MDLHEADMOTORKP=1000
MDLHEADMOTORKI=13
MDLHEADMOTORKD=1056
MDLHEADMOTORAC=2876
MDLHEADMOTORIL=9999
MDLHEADMOTORDS=10
SUPPREPURGEDELAY=0
SUPPREPURGEROLLBACK=0
SPTLONGPURGERATE=24000
SPTLONGPURGETIME=35
SPTLONGPURGERBRATE=96000
SPTLONGPURGERBDIST=0
SPTSTDPURGERATE=28800
SPTSTDPURGETIME=25
SPTSTDPURGERBRATE=96000
SPTSTDPURGERBDIST=-210
SUPPOSTPURGEDELAY=0
SUPADDROLLBACK=-700
IDLEPURGEDELAY=5
TIPIDLETIMEOUT=200
MDLPREPURGEDELAY=0
MDLPREPURGEROLLBACK=0
MDLLONGPURGERATE=48000
MDLLONGPURGETIME=50
MDLLONGPURGERBRATE=96000
MDLLONGPURGERBDIST=-10
MDLSTDPURGERATE=24000
MDLSTDPURGETIME=30
MDLSTDPURGERBRATE=96000
MDLSTDPURGERBDIST=-270
MDLPOSTPURGEDELAY=0
MDLADDROLLBACK=-700
KTEMPERATURETODAC=7
TIMETEMPERATUREINTEGRATION=95 
KPROPORTIONALACTION=30
TDERIVITIVE=4
HOTTEMPERATURE=2800
COOLTEMPERATURE=2700
MDLTEMPTOL=70
MDLHIGHTEMPALARM=3000
MDLLOWTEMPALARM=2299
SUPHOTTEMPERATURE=2500
SUPCOOLTEMPERATURE=2100
SUPTEMPTOL=70
SUPHIGHTEMPALARM=3000
SUPLOWTEMPALARM=2000
SYSTEMREVISION=1
HMRUNTIME=6000

This may be in mm per second?
XAXISPOWER=20000
YAXISPOWER=20000
ZAXISPOWER=22000

GLUELESSRATE=40
GLUELESSACCELERATION=0
ZAXISVELOCITY=0
ZAXISACCELERATION=0
FHCRAWL=0
FHVELOCITY=0
LCLOADSPEED=24000
LCDETECTSPEED=48000
UCBACKOUTSPEED=24000
CASSRETRYLIMIT=3
CASSFAILLIMIT=60
XPURGEPOSITION=0
XBRUSHPOSITION=0
YPURGEPOSITION=0
YBRUSHPOSITION=0
TWBRUSHLEN=0
TWBRUSHWID=0
TWWIPELEN=0
TWWIPEWID=0
TWWIPESTEP=0
MDLSHBLOWEROFFTIME=0         # turn off hb for msec for model
SUPSHBLOWEROFFTIME=0         # turn off hb for msec for support
MDLTEMPSOAKTIME=0            # delay before model purge after reaching temp
SUPTEMPSOAKTIME=0            # delay before support purge after reaching temp
MDLSETBACKTEMP=2550          # model liquifier setback temperature
SUPSETBACKTEMP=1500          # support liquifier setback temperature
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

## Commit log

2018-06-11 more info and graphics
    [altair-config.txt]
2018-06-11 added some pdfs
    [origonal stratasys config file.txt]
2018-06-12 added belt info
2018-06-14 steps per mm and gantry travel added
    [uprint-smoothie-config.txt]
2018-06-14 stepper motor notes
2018-06-24 marlin 2.0
    [Configuration.h, Configuration_adv.h]
2019-01-02 Updates and changes - uPrint firmware finalized
    [Configuration.h, Configuration_adv.h, uprint-smoothie-config.txt]
2019-01-02 cad files of hotend and lcd adapter
    models of e
    [uPrint Front LCD.f3d, uPrint Hotend Adapter.f3d]
2020-03-18 uPrint Added
    [6 to 4 mm adapter.f3d, Configuration.h, Configuration_adv.h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]
2020-03-18 duet config
    [Configuration.h, Configuration_adv.h, bed.g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]
2020-03-18 removed junk
    [Configuration.h, Configuration_adv.h, origonal stratasys config file.txt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]
2020-03-18 add photos
    [config.g]

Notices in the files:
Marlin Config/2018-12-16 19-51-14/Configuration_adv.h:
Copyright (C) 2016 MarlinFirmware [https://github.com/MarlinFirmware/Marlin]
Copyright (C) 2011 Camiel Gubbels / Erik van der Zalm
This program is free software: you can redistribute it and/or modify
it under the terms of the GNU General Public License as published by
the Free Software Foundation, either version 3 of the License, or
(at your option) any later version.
